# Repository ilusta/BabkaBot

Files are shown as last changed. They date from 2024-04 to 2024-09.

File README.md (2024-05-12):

# Banka robot
This repository contains frimware, PCB design and 3D models for creating Banka robot

"Banka" robots are used as moving obstacles in robotics competitions. This obstacles follow black line, changing direction at each white point. Competitor`s robots should follow the same black line from start to finish without touching obstacles. The fastest robot to do so wins.

Working time with middle speed setting ~6cm/s is more than 11 hours.
Working time with high speed setting ~18cm/s is more than 7 hours.

This is 2.0 version

Frimware is written for ATmega 328p with Arduino Nano bootloader

Banka obstacle on the line

## List of components:
In the following table listed main components for building one robot. Only main PCB components are included.
| Position | Quantity | Link |
| --- | --- | --- |
| Mi Power Bank 3 Ultra Compact (PB1022ZM) | 1 | - |
| Pololu 150:1 6V Micro Metal Gearmotor | 4 | [Link](https://www.pololu.com/product/3066) |
| RW2i | 4 | [Link](https://www.pololu.com/product/1127) |
| ATmega328P | 1 | [Link](https://ww1.microchip.com/downloads/en/DeviceDoc/Atmel-7810-Automotive-Microcontrollers-ATmega328P_Datasheet.pdf) |
| DRV8833 | 1 | [Link](https://www.ti.com/lit/ds/symlink/drv8833.pdf?ts=1715452574521&ref_url=https%253A%252F%252Fwww.google.com%252F) |
| CP2102 | 1 | [Link](https://www.silabs.com/documents/public/data-sheets/CP2102-9.pdf) |
| TCRT5000 | 6 | [Link](https://www.vishay.com/docs/83760/tcrt5000.pdf) |

## Instruction
Code can be compiled and uploaded using Arduino IDE. Select Arduino Nano as board type and upload using devug header on the PCB.

* During initialization short animation will be shown on the strip of green LEDs.
* Under normal conditions green LED will blink slowly indicating waiting state. If motor driver error occures (overheat or too high current), red LED will light up indicating error state.
* Robot can be started or stoped using corresponding button. In working state green LED will blink fast. Robot will continuously follow black line between two white dots on it`s center.
* If error occures in working state robot will stop.
* Robot`s speed can be changed between one of 8 levels using corresponding buttons. Current speed is shown on the strip of green LEDs.
* Robot can move alon 3cm or 5 cm line. To switch between line width hold start button for longer than 10 seconds. After 10 seconds current mode will be shown on the strip of green LEDs (two central LEDs - 3cm line, all LEDs except first and last - 5cm)

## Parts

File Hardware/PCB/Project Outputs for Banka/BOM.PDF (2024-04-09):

Comment | Description | Designator | Footprint | LibRef | Quantity
1uF | Конденсатор кер. | C1, C2, C3 | NPC0805 | Capacitor ceramic | 3
12pF | Конденсатор кер. | C4, C6 | NPC0805 | Capacitor ceramic | 2
100nF | Конденсатор кер. | C5 | NPC0805 | Capacitor ceramic | 1
100uF | Конденсатор пол. | C7, C8, C9, C14 | TANTAL CAPACITOR C | Capacitor tantal | 4
10uF | Конденсатор кер. | C11, C12, C13 | NPC0805 | Capacitor ceramic | 3
ATMEGA328P | Микроконтроллер | D1 | TQFP32 | ATMEGA328P | 1
LM7805 | DC-DC преобразователь | D2 | DPAK | LM7805 | 1
DRV8870 | Драйвер моторов | D3, D5 | SOIC8 WITH THERMAL PAD | DRV8870 | 2
74HC595 | Сдвиговый регистр, 8 каналов | D4 | SOIC16 | 74HC595 | 1
TCRT5000 | Инфракрасная оптопара | IC1, IC2, IC3, IC4, IC5, IC6 | TCRT5000 | TCRT5000 | 6
100 | Резистор 0,25Вт | R1, R2, R3, R4, R19, R20, R21, R25, R26, R27 | R0603 | Резистор 0,25Вт | 10
10K | Резистор 0,25Вт | R5, R8, R9, R15, R16, R17, R22, R23, R24, R28, R29, R30, R31, R32 | R0603 | Резистор 0,25Вт | 14
3.3K | Резистор 0,25Вт | R6 | R0603 | Резистор 0,25Вт | 1
1K | Резистор 0,25Вт | R7, R10, R11, R12 | R0603 | Резистор 0,25Вт | 4
1K | Резистор 0,05Вт | R14, R18 | CAT16 | Резисторная сборка 0,05Вт | 2
| Кнопка без фиксации | SB1, SB2, SB3, SB4 | 1-1437565-6 WITH LABEL | Button_SMD | 4
GREEN | Светодиод SMD | VD1, VD3, VD5, VD6, VD7, VD8, VD9, VD10, VD11, VD12 | 0805_LED _GREEN | LED | 10
| Диод | VD2 | SOD123 | Diode | 1
RED | Светодиод SMD | VD4 | 0805_LED _RED | LED | 1
МОТОР 11 | Разъем - 2 конт. вилка | X1 | KLS2-301-5.00 WITH LABEL | Header_2_plg | 1
МОТОР 12 | Разъем - 2 конт. вилка | X2 | KLS2-301-5.00 WITH LABEL | Header_2_plg | 1
ОТЛАДКА | Разъем - 5 конт. вилка | X3 | 5 PADSx2.54 WITH LABEL | Header_5_plg | 1
POWER_IN | Разъем - 2 конт. вилка | X4 | PCB WITH TYPE C PD TRIGGER | Header_2_plg | 1
МОТОР 21 | Разъем - 2 конт. вилка | X5 | KLS2-301-5.00 WITH LABEL | Header_2_plg | 1
МОТОР 22 | Разъем - 2 конт. вилка | X6 | KLS2-301-5.00 WITH LABEL | Header_2_plg | 1
16MHz | Кварцевый резонатор | Z1 | QUARTZ | KX-7T | 1

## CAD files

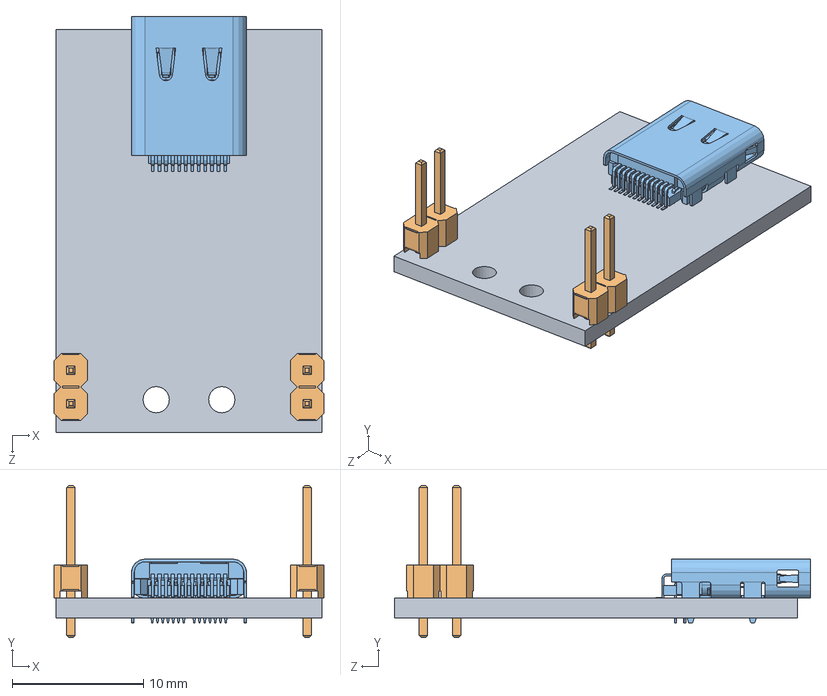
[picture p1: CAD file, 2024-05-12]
Hardware/3D Model/0510-Плата USB type-C/0510-Плата USB type-C.SLDASM
20.5 x 11.6 x 31.7 mm
010510-Плата
PLS-2 x 2
USB Connector Type C female

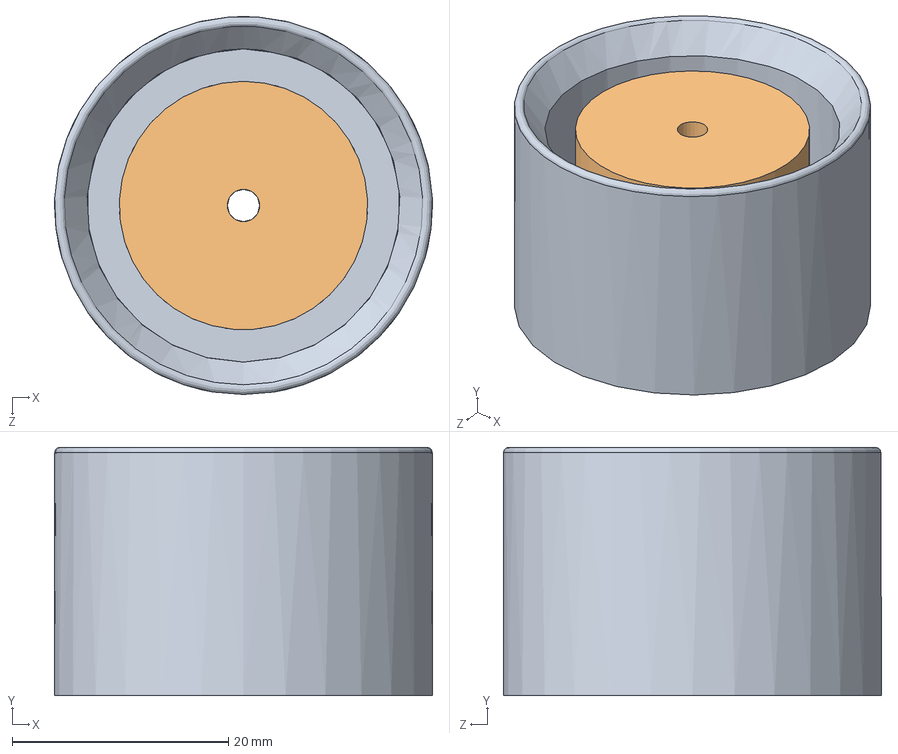
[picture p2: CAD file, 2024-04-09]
Hardware/3D Model/1410-Форма.SLDASM
35.0 x 23.0 x 35.0 mm
1210-Форма
1310-Форма

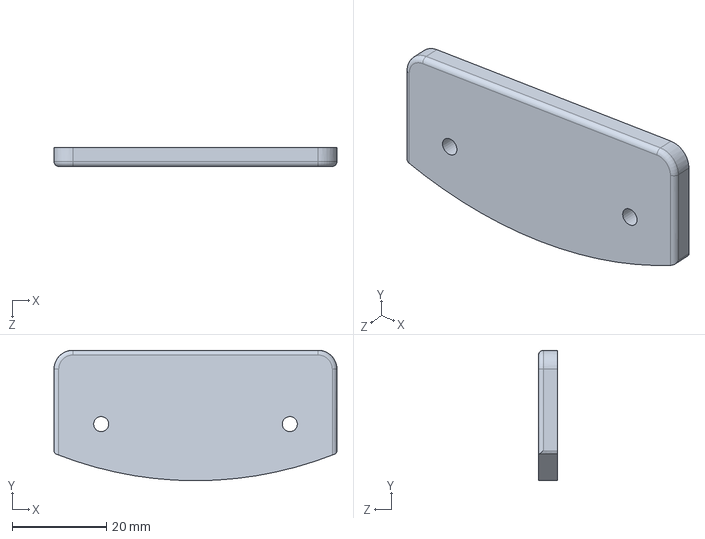
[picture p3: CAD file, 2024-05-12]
Hardware/3D Model/0810-Крышка.SLDPRT
60.0 x 27.6 x 4.00 mm

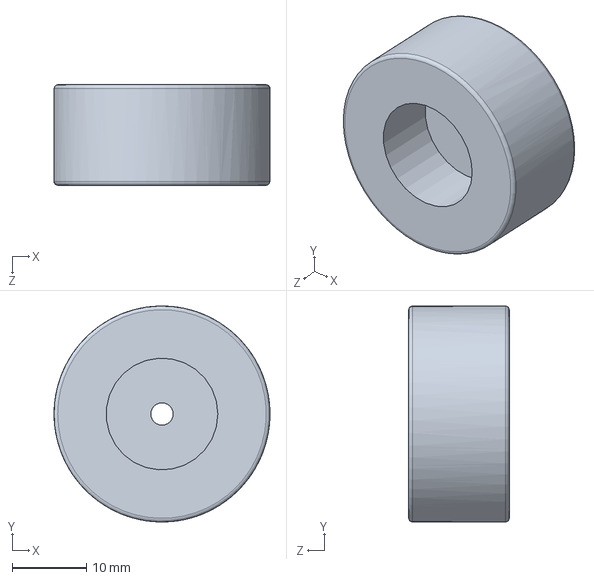
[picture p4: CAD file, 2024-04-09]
Hardware/3D Model/Стандартные/Колесо.SLDPRT
29.0 x 29.0 x 13.5 mm

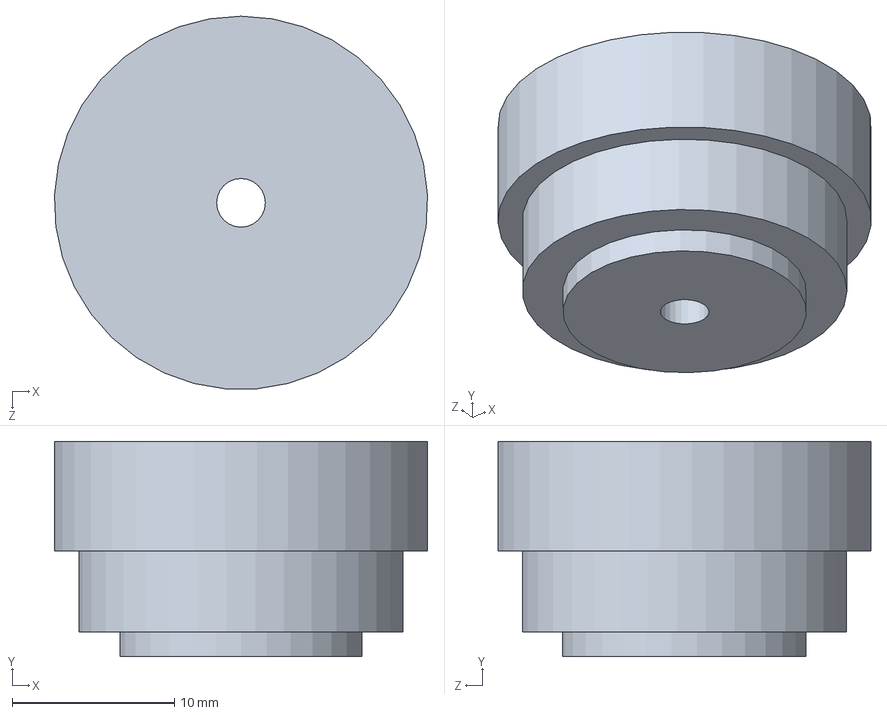
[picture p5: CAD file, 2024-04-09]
Hardware/3D Model/1310-Форма.SLDPRT
23.0 x 13.2 x 23.0 mm

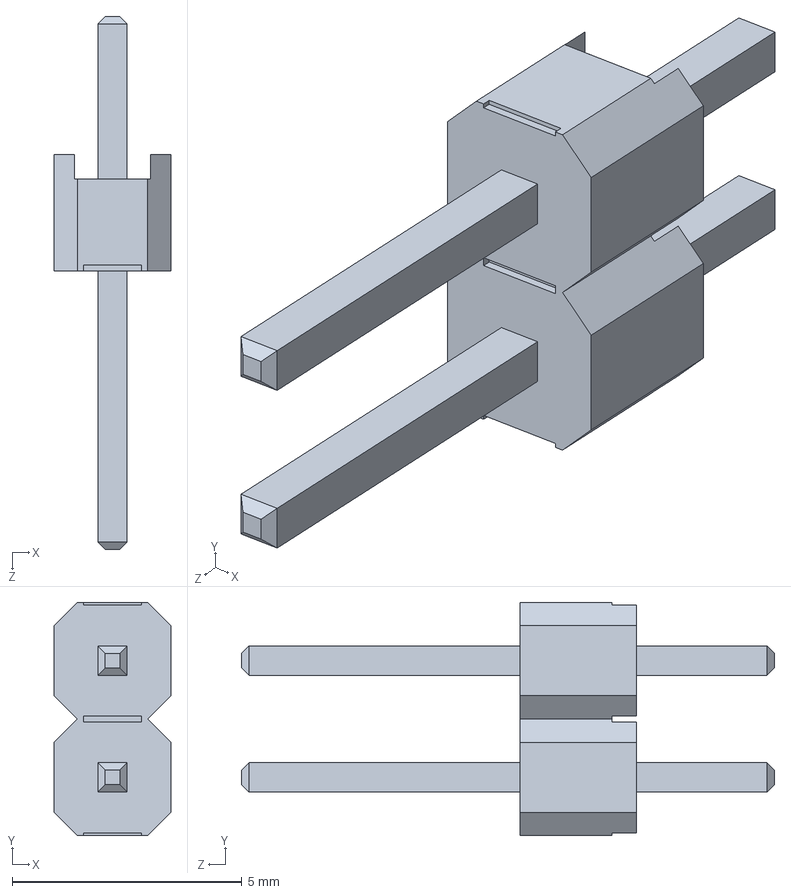
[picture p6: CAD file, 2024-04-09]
Hardware/3D Model/Стандартные/PLS-2.SLDPRT
2.54 x 5.08 x 11.6 mm

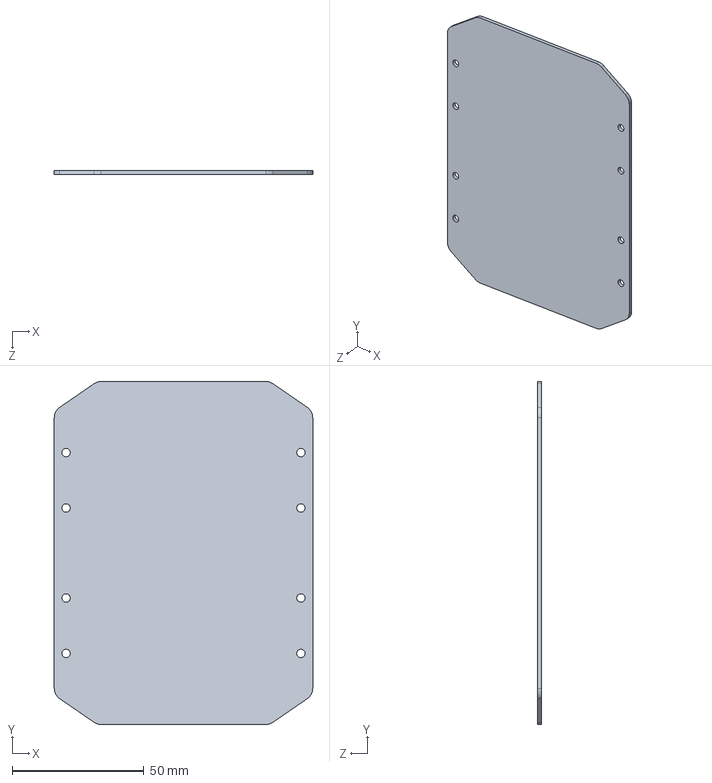
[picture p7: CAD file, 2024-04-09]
Hardware/3D Model/0210-Плата.SLDPRT
98.0 x 130.0 x 1.60 mm

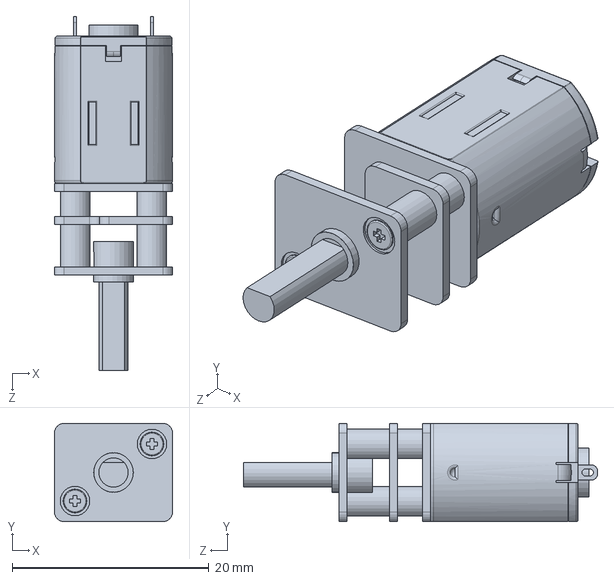
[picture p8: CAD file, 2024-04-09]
Hardware/3D Model/Стандартные/Motor DC 3000RPM.SLDPRT
12.0 x 10.0 x 36.0 mm

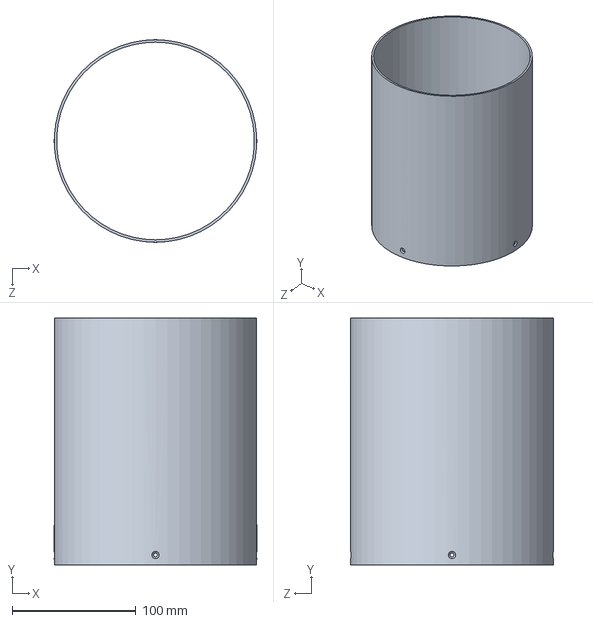
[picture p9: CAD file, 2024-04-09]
Hardware/3D Model/0310-Корпус.SLDPRT
164.0 x 200.0 x 164.0 mm

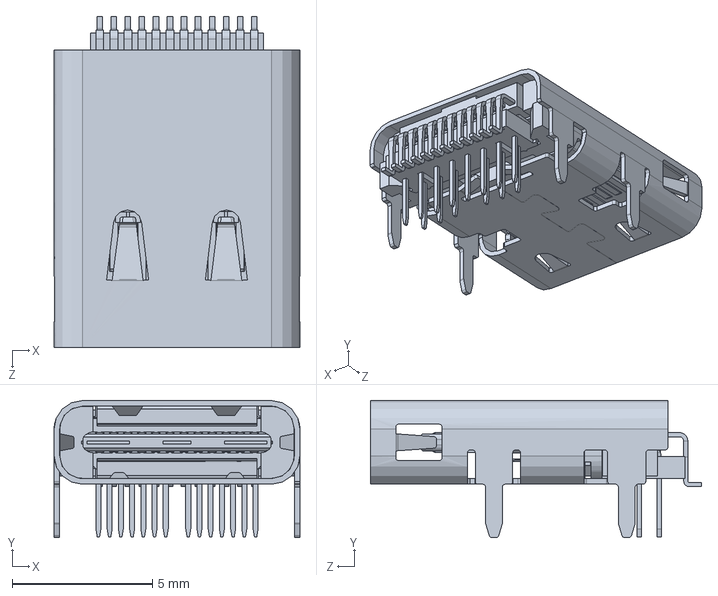
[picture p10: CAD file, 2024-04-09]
Hardware/3D Model/Стандартные/USB Connector Type C female.SLDPRT
8.76 x 4.88 x 11.8 mm

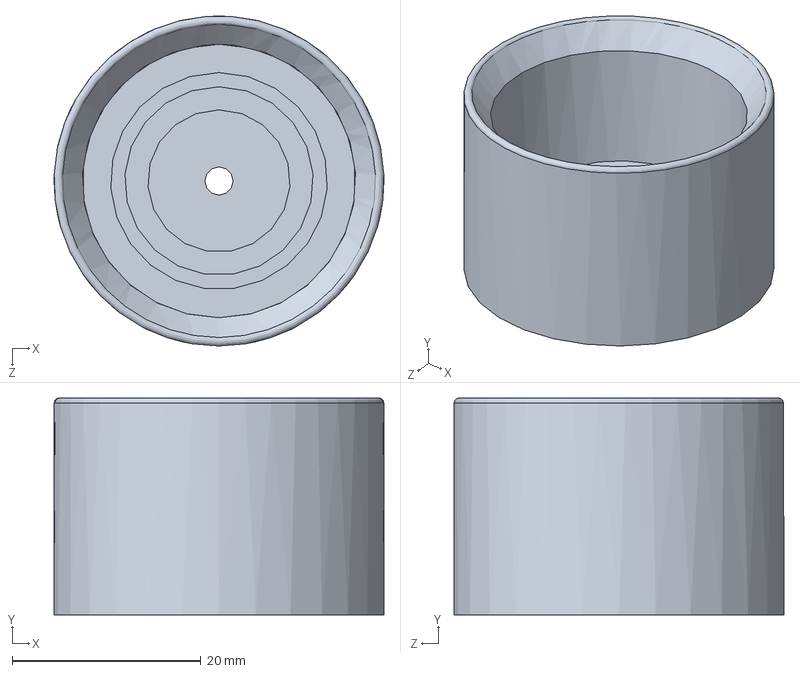
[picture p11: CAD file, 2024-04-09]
Hardware/3D Model/1210-Форма.SLDPRT
35.0 x 23.0 x 35.0 mm

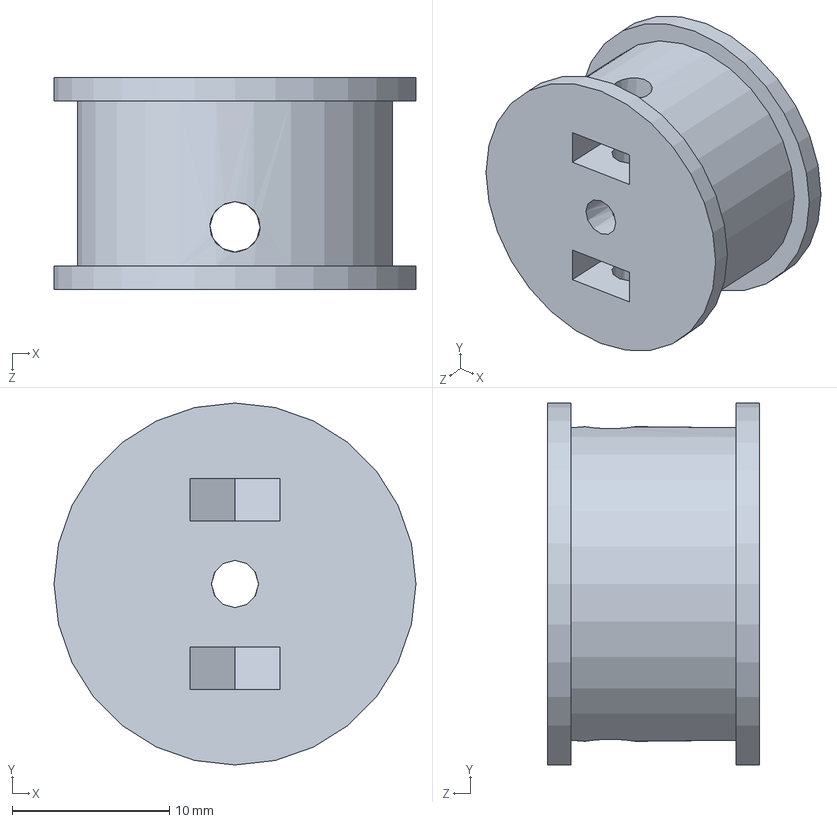
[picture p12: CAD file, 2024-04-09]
Hardware/3D Model/1110-Диск.SLDPRT
23.0 x 23.0 x 13.5 mm

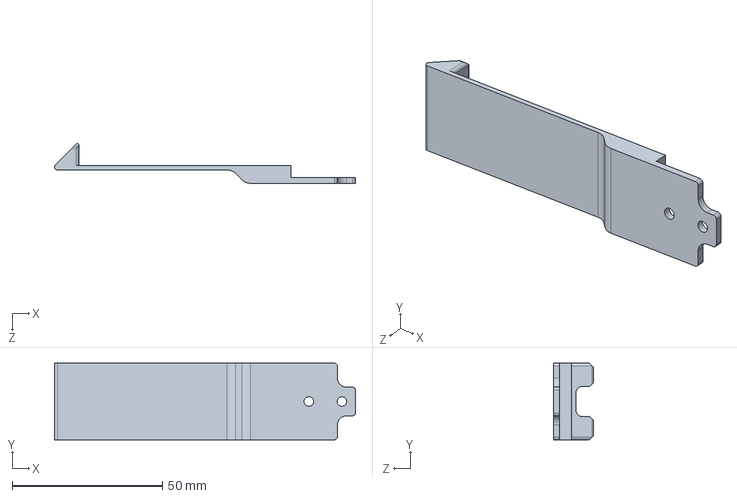
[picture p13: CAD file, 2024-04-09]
Hardware/3D Model/1010-Защёлка.SLDPRT
100.1 x 25.5 x 13.3 mm

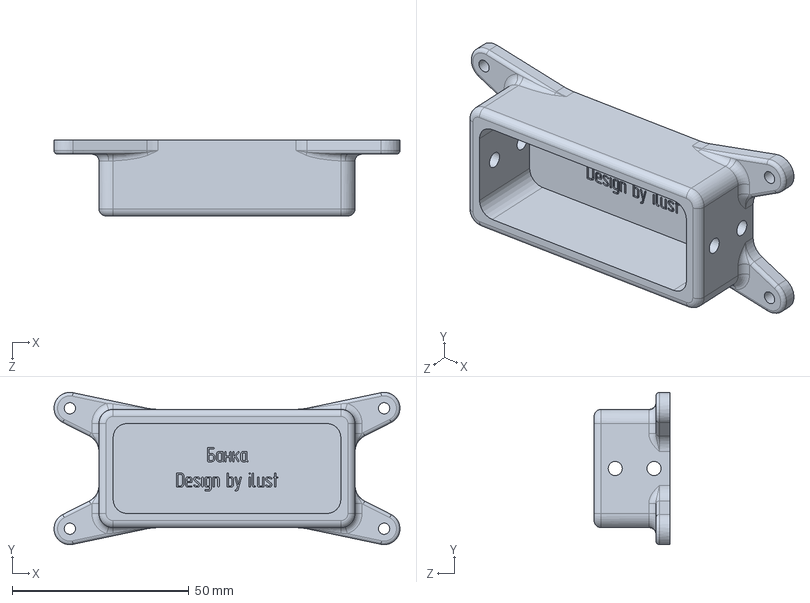
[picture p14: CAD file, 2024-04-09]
Hardware/3D Model/0610-Держатель аккума.SLDPRT
98.0 x 43.1 x 21.5 mm

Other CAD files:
Hardware/3D Model/0910-Крышка.SLDPRT
Hardware/3D Model/0410-Крышка.SLDPRT
Hardware/3D Model/0110-Рама.SLDPRT
Hardware/3D Model/0510-Плата USB type-C/010510-Плата.SLDPRT
Hardware/3D Model/STL/0110-Рама.STL
Hardware/3D Model/STL/0810-Крышка.STL
Hardware/3D Model/STL/0910-Крышка.STL
Hardware/3D Model/STL/1010-Защёлка.STL
Hardware/3D Model/STL/1110-Диск.STL
Hardware/3D Model/STL/1210-Форма.STL
Hardware/3D Model/STL/1310-Форма.STL

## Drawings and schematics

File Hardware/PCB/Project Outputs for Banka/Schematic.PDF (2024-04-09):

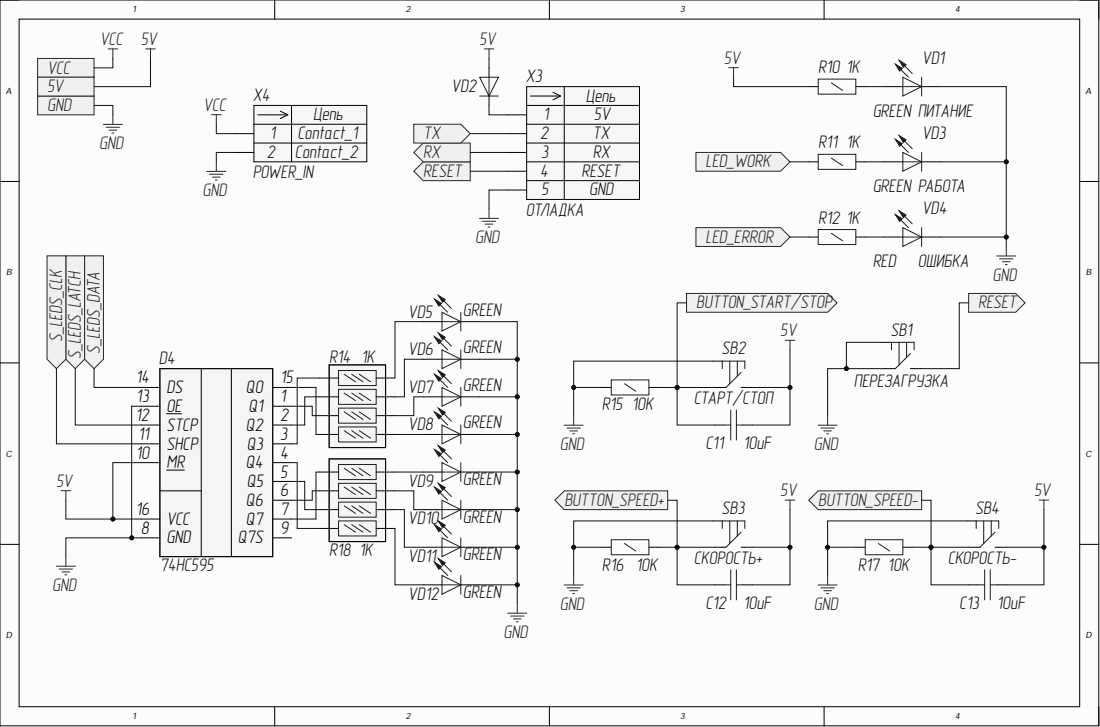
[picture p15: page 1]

4 | RESET
5 | GND

СКОРОСТЬ-

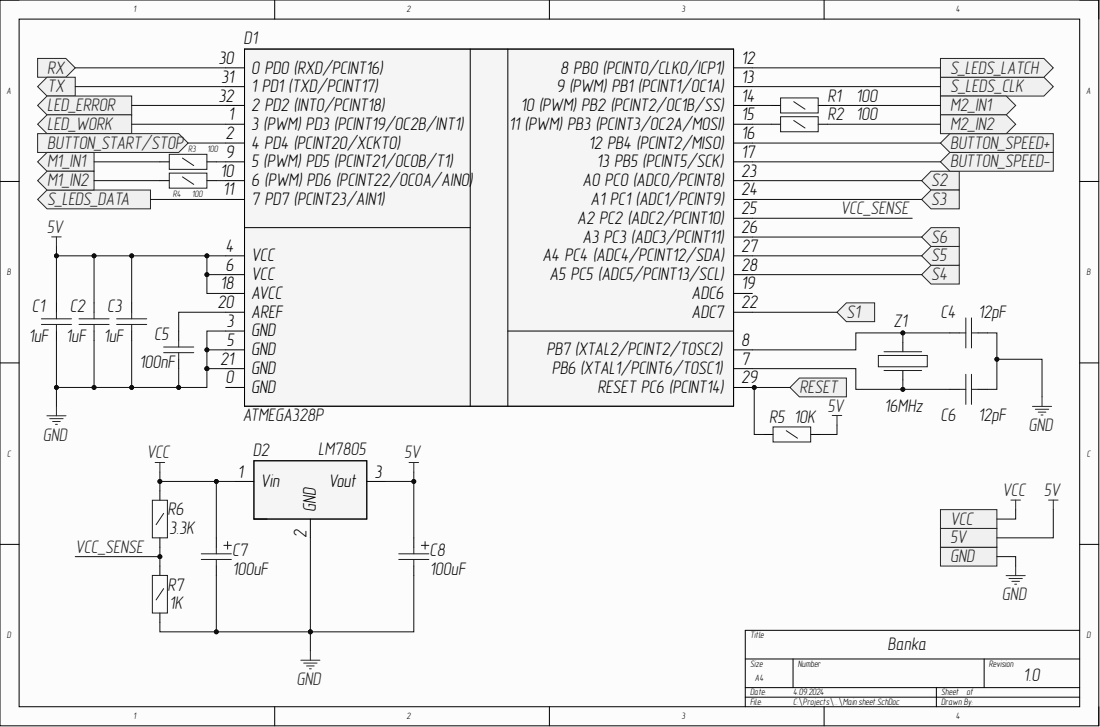
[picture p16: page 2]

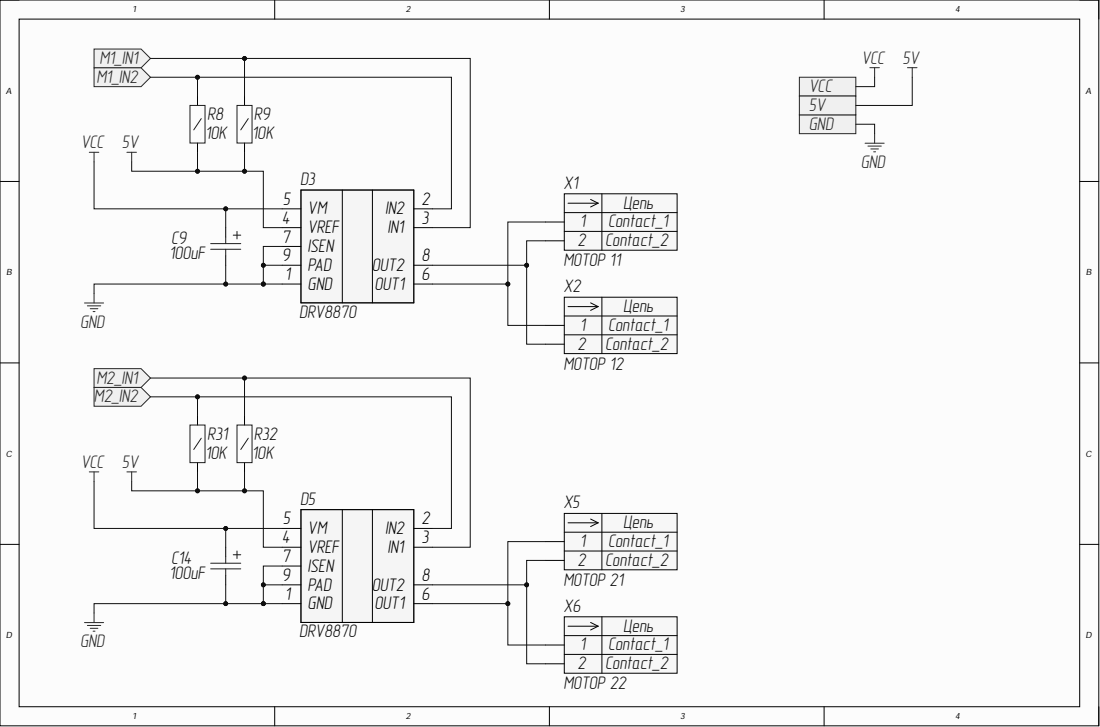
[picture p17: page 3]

Цепь
12 | Contact_1
Contact_2

VM | IN2
4 | | IN1 | 3 VREF
ISEN PAD GND | OUT2 OUT1 | 8

Contact_1

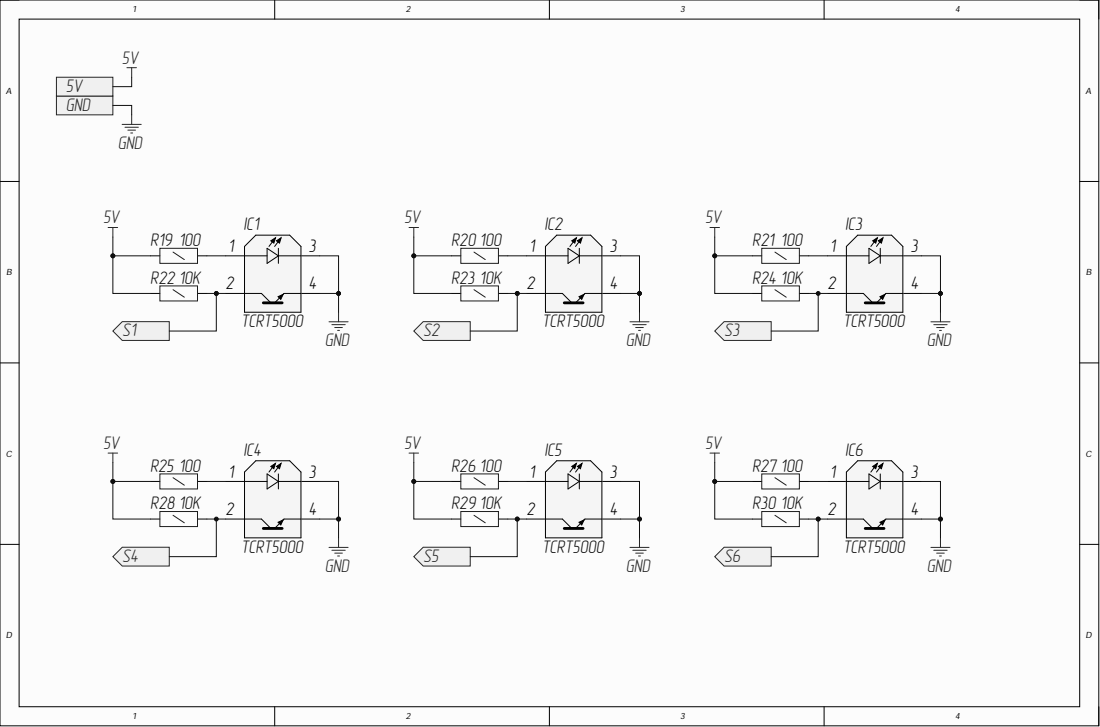
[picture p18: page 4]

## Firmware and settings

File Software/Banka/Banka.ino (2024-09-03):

#include "Robot.h"
#include "Useful.h"
#include <EEPROM.h>

#define KP   0.15
#define KD   5.0
#define CALIBRATION_TIME  10000

#define EEPROM_SPEED      0
#define EEPROM_WIDTH      1
#define EEPROM_TRESHOLDS  2  

#define STATE_WAITING false
#define STATE_MOVING true

Robot robot = Robot();

bool state = STATE_WAITING;
int speed = EEPROM.read(EEPROM_SPEED);
long long widthChangeTimer = millis();
bool width = EEPROM.read(EEPROM_WIDTH);
bool direction = 1;
long long dirTimer = millis();
long long timer = millis();
int val = 0;
int tresholds[6] = {300, 300, 300, 300, 300, 300};
int err = 0, errOld = 0;
int u = 0;
int sp = 0;


void setup() {
  Serial.begin(115200);
  robot.wait(1);

  for(int i = 0; i < 6; i++){
    tresholds[i] = EEPROM.read(EEPROM_TRESHOLDS + i) * 4;
  }

  for (int i = 0; i <= 8; i++) {
    robot.ledArr.write(1 << i);
    delay(50);
  }
  for (int i = 7; i >= 0; i--) {
    robot.ledArr.write(1 << i);
    delay(50);
  }
  robot.ledArr.show(0);
  delay(100);
}

void loop() {
  while(true){
    robot.wait(5);

    if(robot.buttonInc.isPressed() && robot.buttonDec.isPressed()){
      calibration();
      continue;
    }

    bool spFlag = false;
    if (robot.buttonInc.isReleased()) {
      speed++;
      spFlag = true;
      if (speed > 8) speed = 8;
    }
    if (robot.buttonDec.isReleased()) {
      speed--;
      spFlag = true;
      if (speed < 1) speed = 1;
    }
    if (spFlag) EEPROM.write(0, speed);
    robot.ledArr.show(speed);

    if (!robot.buttonStartStop.isPressed()) widthChangeTimer = millis();
    if (millis() - widthChangeTimer > 10000) {
      width = !width;
      EEPROM.write(1, width);
      if (width) robot.ledArr.write(0b01111110);
      else robot.ledArr.write(0b00011000);

      while (robot.buttonStartStop.isPressed()) {
        if (width) robot.ledArr.write((millis() % 1000) > 500 ? 0 : 0b01111110);
        else robot.ledArr.write((millis() % 1000) > 500 ? 0 : 0b00011000);
        robot.wait(1);
      }
      robot.buttonStartStop.isReleased();
      robot.wait(1);
    }
    else if (robot.buttonStartStop.isReleased()) state = !state;

    if (robot.getError()) state = STATE_WAITING;


    if (direction) {
      if (width) {
        val = robot.getSensor(5);
        err = robot.getSensor(5) - tresholds[5];
      }
      else {
        val = robot.getSensor(4);
        err = robot.getSensor(4) - tresholds[4];
      }
    }
    else {
      if (width) {
        val = robot.getSensor(2);
        err = robot.getSensor(2) - tresholds[2];
      }
      else {
        val = robot.getSensor(1);
        err = robot.getSensor(1) - tresholds[1];
      }
    }

    u = err*KP + (err - errOld)*KD/(millis() - timer);
    errOld = err;
    timer = millis();
    if (abs(u) > 100) u = sign(u) * 100;
    sp = map(speed, 1, 8, 40, 180);


    if (state) {
      digitalWrite(LED_WORK, (millis() % 300) < 150);

      if (direction) robot.setMotors(sp + u, sp - u);
      else robot.setMotors(-sp - u, -sp + u);


      if ((!direction && (robot.getSensor(0) < tresholds[0]) || direction && (robot.getSensor(3) < tresholds[3])) && millis() - dirTimer > 1000) {
        direction = !direction;
        errOld = 0;
        dirTimer = millis();
      }

    }
    else {
      if (!robot.getError()) digitalWrite(LED_WORK, (millis() % 1500) > 1400);
      else digitalWrite(LED_WORK, 0);
      robot.stopMotors();
    }

    /*
    Serial.print("Voltage: " + String(robot.getVoltage()));
    Serial.print("  Width: " + String(width ? "5cm" : "3cm"));
    Serial.print("  Direction: " + String(direction ? "forward" : "backward"));
    Serial.print("  Speed: " + String(sp));
    Serial.print("  Val: " + String(val));
    Serial.print("  U: " + String(u));
    Serial.print("  Error: " + String(robot.getError()));
*/
    Serial.print("  Sensors: ");
    for (int i = 0; i < 6; i++)
      Serial.print(String(robot.getSensor(i)) + " ");
    Serial.println();
  }
}

void calibration(){
  Serial.println("Start calibration");

  robot.setMotors(150, -150);
  uint16_t minVal[6];
  uint16_t maxVal[6];
  for(int i = 0; i < 6; i++){
    minVal[i] = 1024;
    maxVal[i] = 0;
  }

  uint32_t calibrationTimer = millis();
  while(millis() - calibrationTimer < CALIBRATION_TIME){
    robot.wait(1);
    robot.ledArr.show(millis()%500 > 250 ? 8 : 0);
    for(int i = 0; i < 6; i++){
      minVal[i] = min(minVal[i], robot.getSensor(i));
      maxVal[i] = max(maxVal[i], robot.getSensor(i)); 
    }
  }
  robot.stopMotors();

  Serial.print("Calibration result: ");
  for(int i = 0; i < 6; i++){
    Serial.print(String(minVal[i]) + " ");
  }
  Serial.println();
  for(int i = 0; i < 6; i++){
    Serial.print(String(maxVal[i]) + " ");
  }
  Serial.println();
  for(int i = 0; i < 6; i++){
    tresholds[i] = (minVal[i] + maxVal[i]) / 2;
    Serial.print(String(tresholds[i]) + " ");
    EEPROM.write(EEPROM_TRESHOLDS + i, tresholds[i]/4);
  }
  Serial.println("");
  delay(500);
}

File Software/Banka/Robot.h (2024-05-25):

#pragma once

#include <Arduino.h>

#include "Button.h"
#include "ConnectionList.h"
#include "LedArray.h"
#include "MotorDriver.h"

#define WRONG_VOLTAGE_MAX_TIME  1000

#define VCC_SENSE_COEF  0.007102


#define VOLTAGE_ERROR   0
#define DRIVER_ERROR    1

class Robot{
    private:
    uint8_t error = false;
    double voltage;
    long long wrongVoltageTimer;
    int sensors[6] = {S1, S2, S3, S4, S5, S6};
    int sensorsVal[6];

    public:
    Button buttonStartStop = Button(BUTTON_START_STOP);
    Button buttonInc = Button(BUTTON_INC);
    Button buttonDec = Button(BUTTON_DEC);

    LedArray ledArr = LedArray(LEDARR_DATA, LEDARR_LATCH, LEDARR_CLK);

    MotorDriver motor1 = MotorDriver(MOTOR1_PIN1, MOTOR1_PIN2);
    MotorDriver motor2 = MotorDriver(MOTOR2_PIN1, MOTOR2_PIN2);

    Robot();
    void wait(int);
    int getSensor(int);
    void stopMotors();
    void setMotors(int, int);
    uint8_t getError();
    double getVoltage();
};


Robot::Robot(){
    //LEDs
    pinMode(LED_ERROR, OUTPUT);
    pinMode(LED_WORK, OUTPUT);

    //Sensors
    for(int i = 0; i < 6; i++)
        pinMode(sensors[i], INPUT);

    //Voltage sense
    pinMode(VIN_SENSE, INPUT);

    //Motor driver fault pin
    pinMode(MOTOR_FAULT_PIN, INPUT_PULLUP);
}

void Robot::wait(int delayTime){
    long long timer = millis();

    do {
        buttonStartStop.update();
        buttonInc.update();
        buttonDec.update();
        motor1.update();
        motor2.update();

        for(int i = 0; i < 6; i++)
            sensorsVal[i] = analogRead(sensors[i]);
 
        long result;
        // Read 1.1V reference against AVcc
        ADMUX = _BV(REFS0) | _BV(MUX3) | _BV(MUX2) | _BV(MUX1);
        delay(2); // Wait for Vref to settle
        ADCSRA |= _BV(ADSC); // Convert
        while (bit_is_set(ADCSRA,ADSC));
        result = ADCL;
        result |= ADCH<<8;
        result = 1126400L / result; // Back-calculate AVcc in mV
        voltage = result / 1000.0;

        //voltage = analogRead(VIN_SENSE)*VCC_SENSE_COEF;
        if(voltage > 4.5 && voltage < 5.5) wrongVoltageTimer = millis();
        
        error &= ~(1 << VOLTAGE_ERROR);
        if(millis() - wrongVoltageTimer > WRONG_VOLTAGE_MAX_TIME) error |= (1 << VOLTAGE_ERROR);

        error &= ~(1 << DRIVER_ERROR);
        if(!digitalRead(MOTOR_FAULT_PIN)) error |= (1 << DRIVER_ERROR);

        digitalWrite(LED_ERROR, error);
    } while(millis() - timer < delayTime);
}

int Robot::getSensor(int index){
    return sensorsVal[index];
}

void Robot::setMotors(int speed1, int speed2){
    motor1.setSpeed(speed1);
    motor2.setSpeed(-speed2);
}

void Robot::stopMotors(){
    motor1.stop();
    motor2.stop();
}

uint8_t Robot::getError(){
    return error;
}

double Robot::getVoltage(){
    return voltage;
}

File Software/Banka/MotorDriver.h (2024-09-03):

#pragma once

#include <Arduino.h>

#include "Useful.h"


#define ACCELERATION 3


class MotorDriver{
    private:
    int pin1, pin2;
    double speed = 0;
    double prevSpeed = 0;
    long long timer = 0;

    public:
    MotorDriver(int, int);
    void stop();
    void setSpeed(int);
    void update();
};

MotorDriver::MotorDriver(int pin1, int pin2){
    this->pin1 = pin1;
    this->pin2 = pin2;

    pinMode(pin1, OUTPUT);
    pinMode(pin2, OUTPUT);

    digitalWrite(pin1, 1);
    digitalWrite(pin2, 1);
}

void MotorDriver::setSpeed(int speed){
  this->speed = speed;
}

void MotorDriver::stop(){
  speed = 0;
  prevSpeed = 0;
  digitalWrite(pin1, 1);
  digitalWrite(pin2, 1);
}

void MotorDriver::update(){

    if(abs(speed - prevSpeed) < ACCELERATION*2) prevSpeed = speed;
    prevSpeed = prevSpeed + sign(speed - prevSpeed) * (millis() - timer) * ACCELERATION;
    int sp = prevSpeed;
    //int sp = speed;
    timer = millis(); 
  
    bool dir = true;
    
    if(sp < 0) dir = false;
    sp = abs(sp);
    if(sp > 255) sp = 255;

    if(dir){
        digitalWrite(pin1, 1);
        analogWrite(pin2, 255-sp);
    }
    else {
        digitalWrite(pin2, 1);
        analogWrite(pin1, 255-sp);
    }
}

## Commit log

2024-04-09 Added hradware files
    [010510-Плата.SLDPRT, 0110-Рама.SLDPRT, 0110-Рама.STL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]
2024-04-10 PCB v2.0
    [Banka.PrjPcb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]
2024-05-12 3D model updated to 2.0 version
    [0510-Плата USB type-C.SLDASM, 0810-Крышка.SLDPRT]
2024-05-25 Calibration added
2024-05-25 Files added
    [0810-Крышка.SLDPRT]
2024-09-03 Fixed motor noise in stationary state
    [MotorDriver.h]
2024-09-03 Changed calibration movement
